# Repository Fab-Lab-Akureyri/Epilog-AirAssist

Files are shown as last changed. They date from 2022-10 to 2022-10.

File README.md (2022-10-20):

# Epilog-AirAssist
Upgrade the air assist system for Epilog laser cutter, for a better sound environment. 

## Intro

For years staff and students within the Fab Lab here in Akureyri have been slowly going insane. There are multiple reasons for this of course, but one of which is the constant `CHK-CHK-CHK-CHK` sound of the recommended air assist pumps that go with our Epilog laser cutting machines we have. 

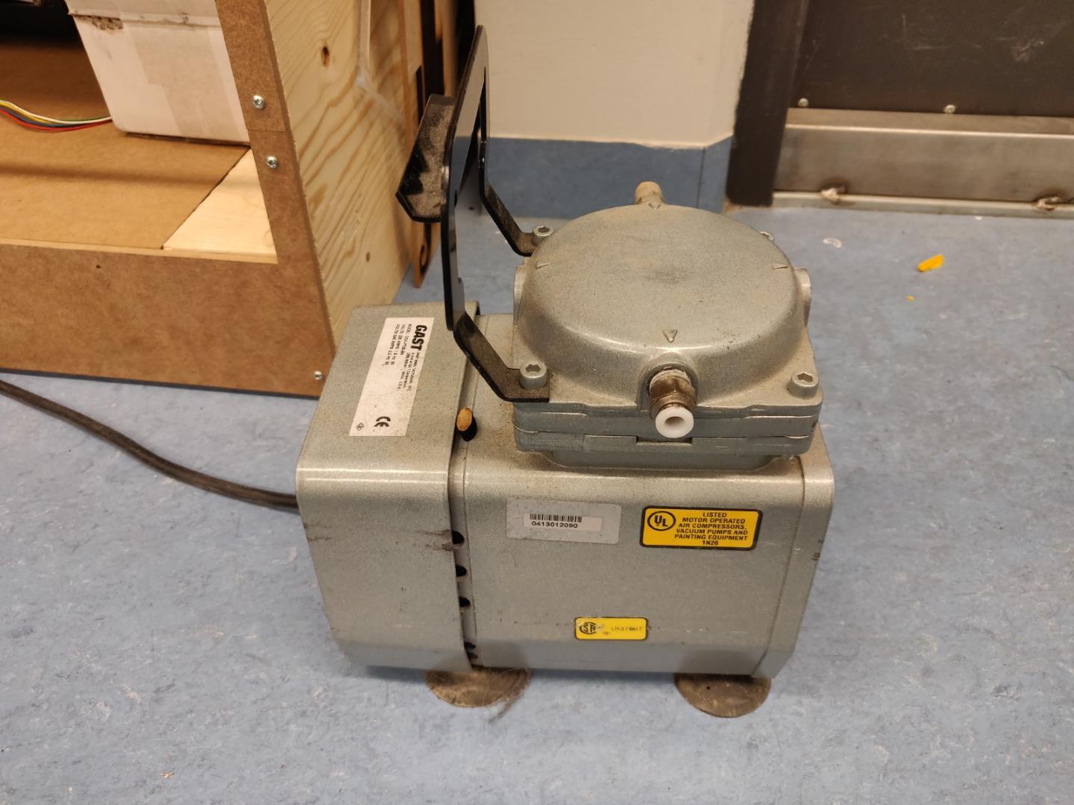
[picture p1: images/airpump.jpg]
Air assist pump


## Investigation

Driven to despair, I decided to take a closer look at the air assist system. 

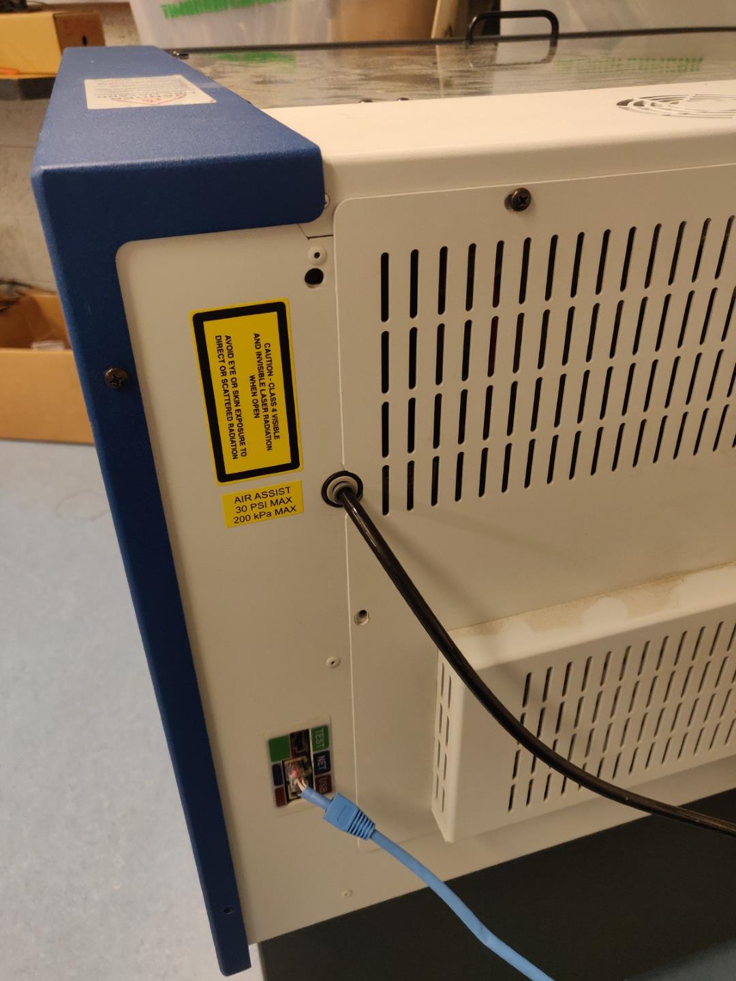
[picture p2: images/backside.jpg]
Backside


Let's zoom in a little closer: 

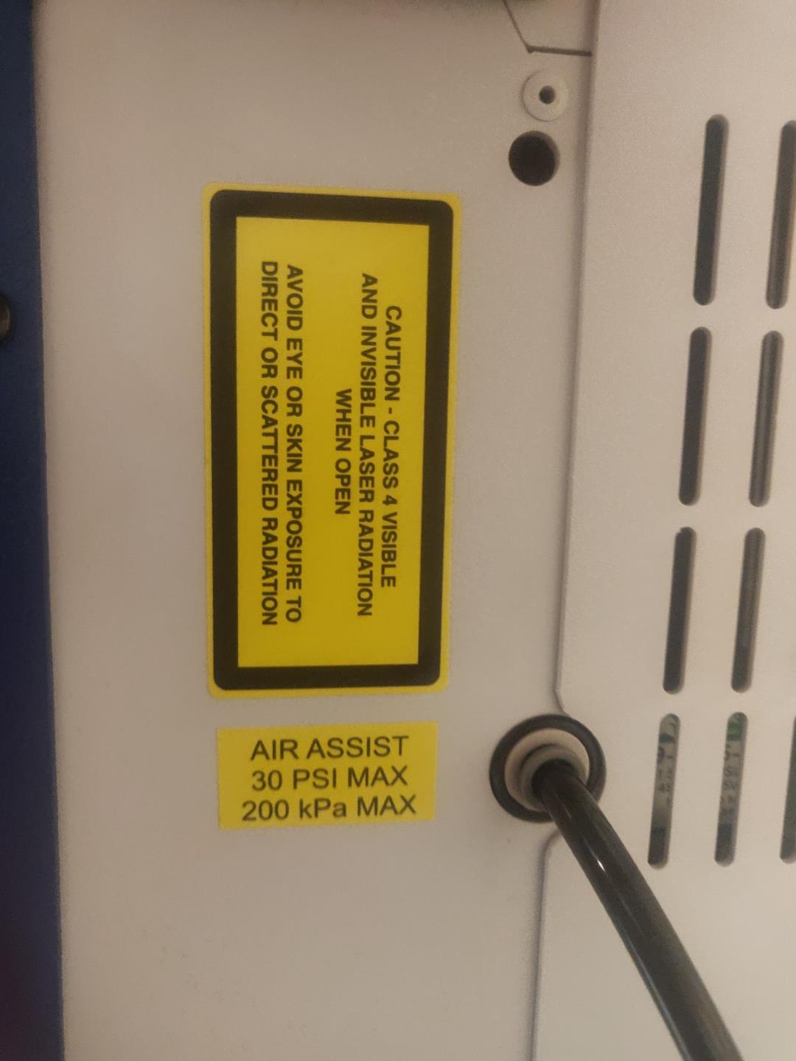
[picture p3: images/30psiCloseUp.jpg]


Relevant information shown here: `30 PSI MAX`

When I removed the backplate form the cutter, I found this air valve/solenoid: 

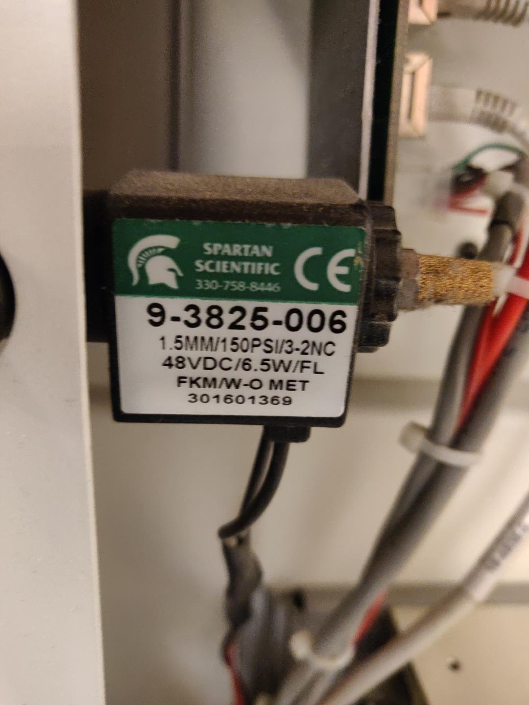
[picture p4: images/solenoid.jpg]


## Operation of the valve

The default operation is to let the air escape freely through the outlet when the machine is not cutting. Once the machine starts cutting, the solenoid is engaged and the air passes to the nozzle. 

This means the pump is constantly running, consuming electricity and generating noise. 

## Remedy

- Block the outlet of the air valve
- Replace the pump(s) with a compressor
- Adjust the output pressure of the compressor

### Air valve

I blocked the outlet, use a 0.19 inch bolt with 10-36 thread. 

Carefully remove the outlet bolt and transfer the rubber gasket to your new bolt. Re-insert the bolt. 

I did not have imperial bolts available, so I [3D printed one](/files/10-36.stl). They hold but I would recommend you get the correct fitting bolt if you can. 

Or you can just fill the silencer bolt with a sealant, such as a hot glue gun. 

### Compressor

I bought a small, relatively quiet compressor: [Stanley Fatmax Silent Air Compressor](https://www.bigdug.co.uk/workshop-flooring-c348/workshop-c11614/air-compressors-c48481/direct-drive-compressors-c82087/stanley-fatmax-silent-air-compressor-dst101-8-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). It's a hobby compressor but seems to be able to satisfy two lasercutters at a time. For a larger setup, you might need a more powerful system. 

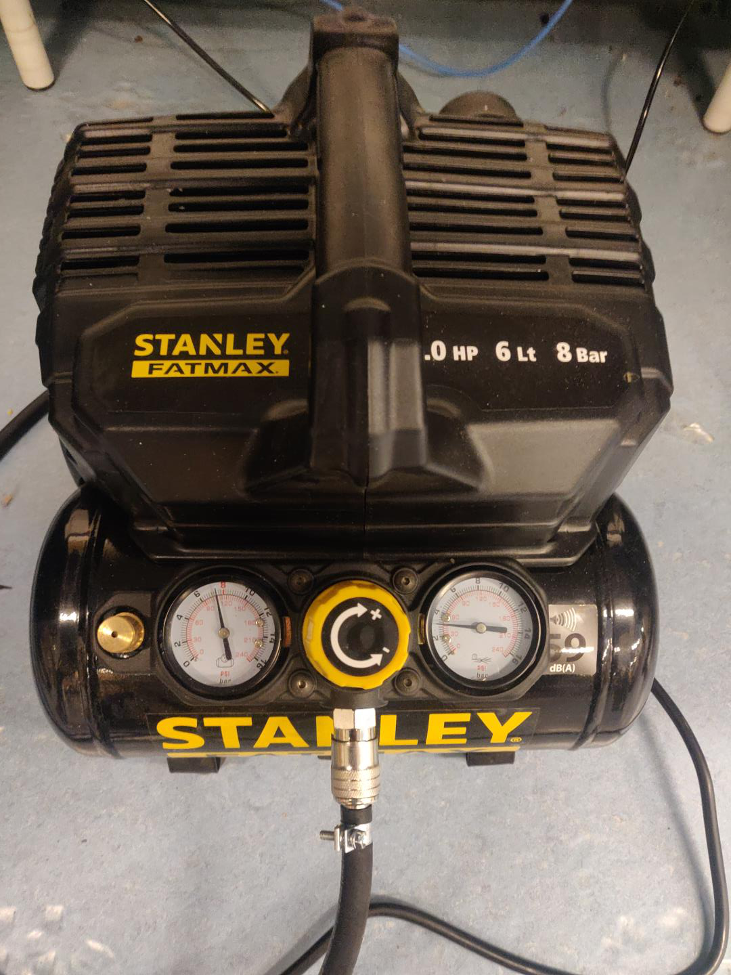
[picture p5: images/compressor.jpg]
Compressor


The air valve accepts 6mm (outer) diameter air lines. 

Using the appropriate fittings and T-connector, attach your compressors output to your machines. 

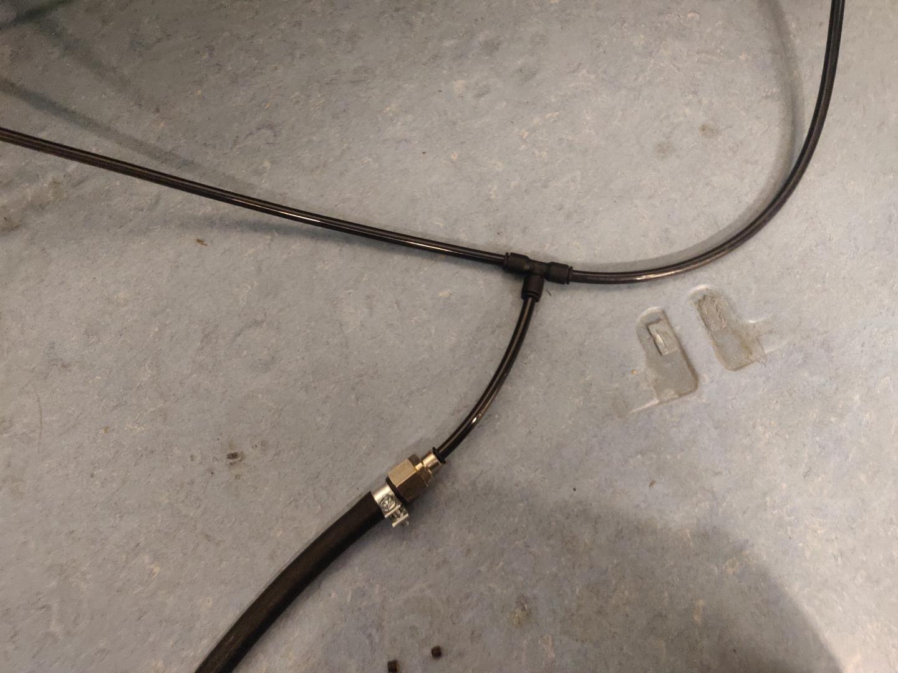
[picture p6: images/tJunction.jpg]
Fittings


Adjust the pressure regulator to output 30PSI and you are all set. 

Enjoy your improved sanity!

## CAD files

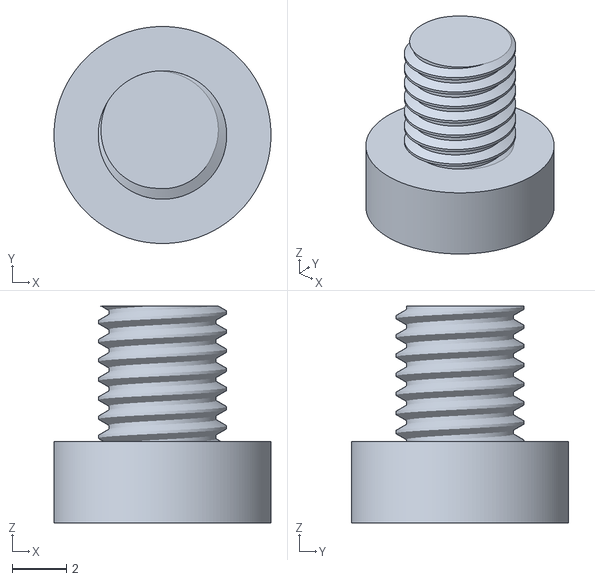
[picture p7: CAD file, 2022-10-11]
files/10-36.stl
8.00 x 8.00 x 8.00
